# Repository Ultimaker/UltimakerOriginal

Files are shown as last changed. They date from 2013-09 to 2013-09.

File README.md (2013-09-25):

UltimakerOriginal
=================

In this repository you will find the documentation and source files for all parts in the Ultimaker-Original 3D printer. All parts are numbered. The BOM (bill of materials) directory should be your start point to find the files you need, as the BOM contains part numbers with amounts and names.
If you are missing a part or information feel free to file an issue on github.

Harma Woldhuis
Ultimaker Research and Development

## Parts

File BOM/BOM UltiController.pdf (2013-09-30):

Total quantity parts | 34
Partnummer | Naam | Quantity
1089 A2P | A | Right Side Controller | 1
1092 A2P | A | Left Side Controller | 1
1093 A2P | A | Bottom Cover Controller | 1
1095 A2P | A | Top Cover Controller | 1
1099 A1P | A | Flatcable 10 wire | 2
1129 A1P | A | Knob | 1
1135 Z1P | A | Spacer, white, 3.2x6x15 | 4
1146 Z1P | A | Ultipanel Rev 1.1 | 1
1202 Z1P | A | ISO 7380 M3x10 | 6
1207 Z1P | A | ISO 7380 M3x25 | 4
1209 Z1P | A | Nut M3 | 10
1248 Z1P | A | SD card | 1

## Ulticontroller

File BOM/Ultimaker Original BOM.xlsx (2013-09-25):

BOM | Ultimaker Original
Total quantity parts | 578
Partnummer |  |  | Naam | Quantity
1002 | A2P | A | Front Panel | 1
1003 | A2P | A | Back Panel | 1
1004 | A2P | A | Left Panel | 1
1005 | A2P | A | Right Panel | 1
1006 | A2P | A | Top Panel | 1
1007 | A2P | A | Bottom Panel | 1
1008 | A2P | A | Reel Holder Part A | 1
1009 | A2P | A | Reel Holder Mounting Plate | 1
1011 | A2P | A | Y-linear shaft | 2
1012 | A2P | A | X-linear shaft | 2
1013 | A2P | A | Feeder Base Plate Non Motor Side | 1
1014 | A1P | A | Trapezoidal Lead Nut | 1
1015 | Z1P | A | Linear Bearing LM12LUU | 2
1016 | Z1P | A | Feeder Quick Fit Coupling | 1
1017 | Z1P | A | Feeder Motor | 1
1018 | A2P | A | Feeder Base Plate Motor Side | 1
1021 | Z1P | A | Ball Bearing 688-2RS | 10
1023 | Z1P | A | Limit Switch, Black Long Wire | 1
1024 | Z1P | A | Limit Switch, Black Short Wire | 1
1025 | Z1P | A | Limit Switch, Blue Wire | 2
1026 | Z1P | A | Limit Switch, Red Wire | 2
1027 | A1P | A | Rigid Shaft Coupling | 1
1028 | A2P | A | Z-linear Shaft | 2
1029 | A2P | A | Bearing Cap Outside | 8
1031 | A2P | A | Feeder Bolt Clip | 1
1032 | A2P | A | Feeder Clamp A | 1
1033 | A2P | A | Feeder Clamp C | 1
1034 | A2P | A | Feeder Clamp B
1035 | A2P | A | Feeder Lever | 1
1036 | A2P | A | Feeder Wheel | 1
1037 | A2P | A | Print Head Coupling Plate | 1
1038 | A2P | A | Print Table Lock Nut | 4
1039 | A2P | A | Feeder U bar | 1
1041 | A2P | A | Feeder Small Gear | 1
1042 | A2P | A | Cable Strain Relief | 1
1043 | A2P | A | Trapezoidal Lead Screw | 1
1044 | A2P | A | Z-shaft Cap Top | 2
1045 | A2P | A | Bearing Cap Inside | 2
1046 | A2P | A | Print Head Shaft X,Y | 2
1047 | A2P | A | Electronics Base Plate | 1
1048 | A2P | A | Print Head Hot End Holder | 1
1049 | A2P | A | Aluminum Heater Block | 1
1052 | Z1P | A | Heater Cartridge 18V 40W | 1
1053 | A2P | A | Hot End Isolator Tube | 1
1054 | A2P | A | Nozzle 0.4mm | 1
1055 | A2P | B | Hot End Isolator Coupler | 1
1056 | A2P | B | Sintered Bushing | 4
1057 | A2P | B | Z-shaft Cap Bottom | 2
1058 | A2P | B | Print Head Back | 1
1059 | A2P | B | Print Head Top Cap | 1
1061 | A2P | B | Print Head Bottom Cap | 1
1062 | A2P | B | Print Head Left | 1
1063 | A2P | B | Print Head Front | 1
1064 | A2P | B | Print Head Right | 1
1065 | Z1P | A | Linear Bearing LM6LUU | 2
1066 | Z1P | A | Hexagon Spacer, White, M3x5.5x12 | 4
1067 | Z1P | A | PEEK Isolator | 1
1068 | Z1P | A | Thermocouple Board Spacer | 1
1069 | Z1P | A | Tube Coupling Collet | 1
1071 | Z1P | A | Clamp Clip | 1
1072 | Z1P | A | Thermocouple Transmitter | 1
1073 | Z1P | A | Thermocouple Sensor | 1
1074 | Z1P | A | Print Head Thumb Screw | 1
1075 | Z1P | A | Print Head Fan 12VDC 1,2W | 1
1076 | Z1P | A | Electronics Cooling Fan 24VDC | 1
1078 | A2P | A | Fan Duct Electronics | 1
1079 | A2P | B | Fan Duct Print Head | 1
1081 | Z1P | A | Z-Motor | 1
1082 | Z1P | A | X,Y-Motor | 2
1083 | Z1P | A | X,Y Motor Spacer Black 3.2x6x11 | 8
1084 | Z2P | A | Timing Pulley 5mm Shaft | 2
1085 | Z1P | A | Timing Belt B100 MXL | 2
1086 | Z1P | A | Timing Belt B300 MXL | 4
1087 | Z2P | A | Bowden Tube | 1
1088 | Z2P | A | Timing Pulley 8mm Shaft | 10
1090 | A1P | A | Arduino Mega Ultimaker Shield 1.5.7 | 1
1094 | A1P | A | Arduino Mega 2560 | 1
1096 | A1P | A | Power Adapter 19v-120W | 1
1097 | A1P | A | Spiral Sleeve | 1
1098 | A1P | A | Stepper Driver | 4
1101 | A2P | A | Print Table Front Plate | 1
1102 | A2P | A | Print Table Back Plate | 1
1103 | A2P | A | Trapezoidal Lead Nut Holder | 2
1104 | A2P | A | Print Table Bottom Plate | 1
1105 | A2P | A | Print Table Arm Part A | 1
1106 | A2P | A | Print Table Arm Part B | 1
1107 | A2P | A | Print Table Arm Part C1 | 4
1108 | A2P | A | Print Table Arm Part D1 | 2
1109 | A2P | A | Print Table Arm Part C2 | 4
1111 | A2P | A | Print Table Arm Part D2 | 2
1112 | A2P | A | Print Table Arm Part E | 1
1113 | A2P | A | Print Table Arm Part F | 1
1114 | A2P | A | Build Platform Acryllic | 1
1116 | A2P | A | Reel Holder Part B | 4
1117 | A2P | A | Sliding Block Part A | 8
1118 | A2P | A | Sliding Block Part B | 1
1119 | A2P | A | Sliding Block Part C | 2
1121 | A2P | A | Sliding Block Part D | 4
1122 | A2P | A | Sliding Block Part E | 1
1123 | A2P | A | Electronics Cover Plate | 1
1126 | A2P | A | Feeder Middle Plate | 1
1127 | Z1P | A | Table Spring D1450 | 1
1128 | A2P | A | Feeder Big Gear | 1
1131 | A2P | A | Cable Duct Front | 2
1132 | A2P | A | Cable Duct Back | 2
1133 | Z2P | A | Feeder Knurled Bolt | 1
1134 | Z1P | A | Capnut M8 | 1
1136 | Z1P | A | Washer M8 | 3
1137 | Z1P | A | Nut M8 | 1
1139 | Z1P | A | Spacer, White, 3.2x5x16 | 4
1141 | Z1P | A | Lock Nut M3 | 11
1142 | Z1P | A | Ball Bearing 693ZZ | 1
1143 | Z1P | A | Feeder Spring D2110 | 1
1144 | Z1P | A | USB Cable | 1
1145 | A2A | A | Main Cable | 1
1147 | Z1P | A | Power Cable EU Type C6
1148 | Z1P | A | Power Cable UK Type C6
1149 | Z1P | A | Power Cable AU Type C6
1150 | Z1P | A | Power Cable US Type C6
1201 | Z1P | B | Washer Large M3 | 7
1202 | Z1P | B | ISO 7380 M3x10 | 45
1203 | Z1P | B | ISO 7380 M3x12 | 5
1204 | Z1P | B | ISO 7380 M3x16 | 67
1206 | Z1P | B | ISO 7380 M3x20 | 12
1207 | Z1P | B | ISO 7380 M3x25 | 1
1208 | Z1P | B | ISO 7380 M3x30 | 53
1209 | Z1P | B | Nut M3 | 151
1211 | Z1P | A | Set Screw M4x4 | 12
1212 | Z1P | A | Set Screw M3x5 | 5
1225 | Z1P | A | tape | 1
1226 | Z1P | A | grease | 1
1227 | Z1P | A | Hex Key Srewdriver 2 | 1
1400 | Z1P | A | Hex Key Wrench 1.5 | 1

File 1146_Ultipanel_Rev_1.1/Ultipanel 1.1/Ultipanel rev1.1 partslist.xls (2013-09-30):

Part | RS partno | Manufacturer partno | Value | Device | Package | Remarks
724-3175 | 724-3175 | RS 724-3175 |  |  |  | buzzer
DS1 | 532-6818 | Displaytech 204A-CC-BC-3LP |  |  |  | lcd screen Blue/White, soldered with header 2.54 mm
EC11E15244B2 | 729-5609 | ALPS EC11E15244B2 |  |  |  | 20mm Vertical encoder 15 Pulses 30 DET
EXP1 | 473-8349 | TE connectivity 1-1634689-0 |  |  |  | right angle!
EXP2 | 473-8349 | TE connectivity 1-1634689-0 |  |  |  | right angle!
HRS163_REVERSE | 685-0788 | Hirose DM1B-DSF-PEJ(82)
R3 | 731-2883 | Panasonic EVM3YSX50B14 | 10K
RBEEP | 708-6014 |  | 440R |  | 0805
RLED | 721-9725 |  | 68R |  | 1206
SHIFT | 483-6544P | NXP 74HC4050D | 4050D |  |  | levelshifter
T4 | 294-312 | Magnatec 2N3904 | 2N3904
JP1 | not used

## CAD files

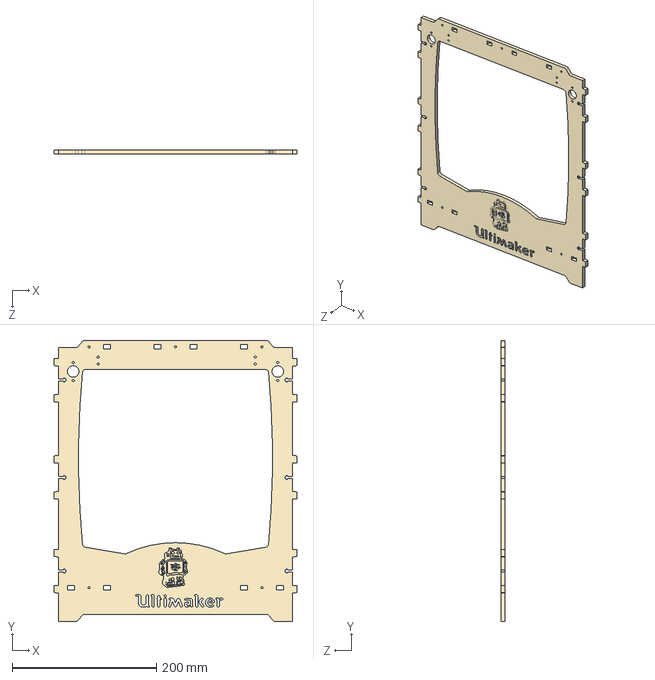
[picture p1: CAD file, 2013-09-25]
1002_Front_Panel/1002-A2P-A.STEP
337.2 x 390.0 x 6.00 mm

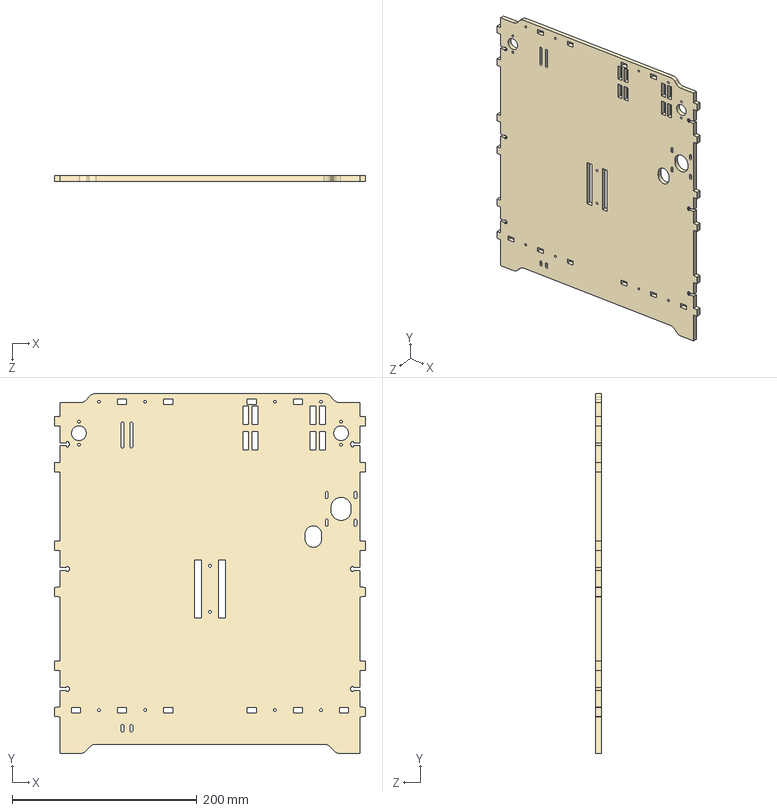
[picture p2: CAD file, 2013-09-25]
1003_Back_Panel/1003-A2P-A.STEP
337.2 x 390.0 x 6.00 mm

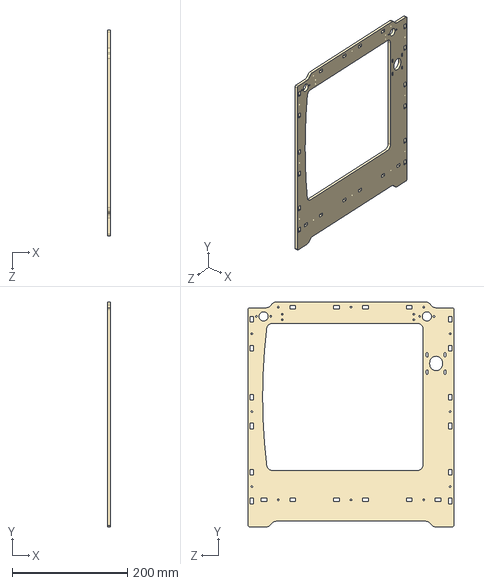
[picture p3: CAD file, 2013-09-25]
1004_Left_Panel/1004-A2P-A.STEP
6.00 x 390.0 x 357.0 mm

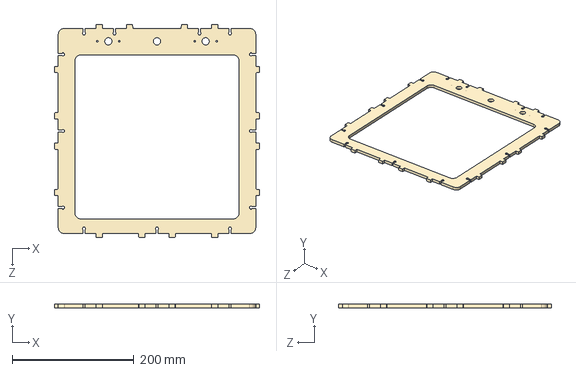
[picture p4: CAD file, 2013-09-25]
1006_Top_Panel/1006-A2P-A.STEP
337.2 x 6.00 x 349.7 mm

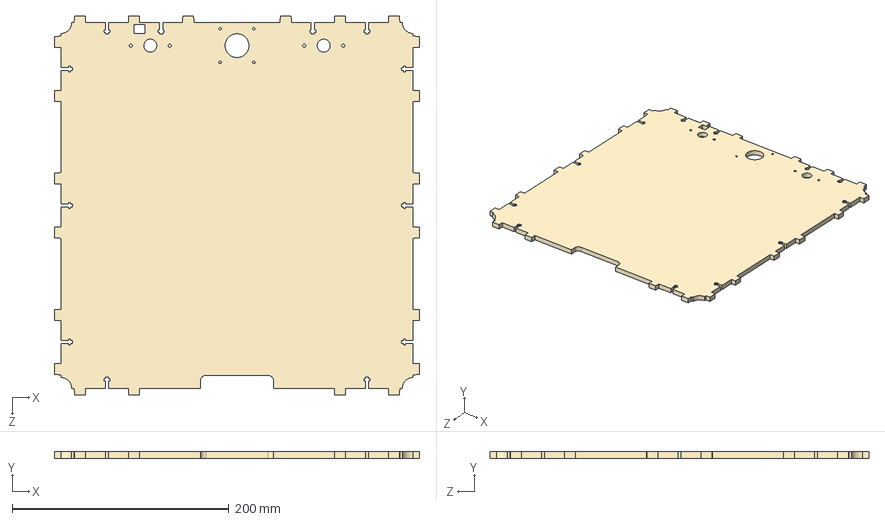
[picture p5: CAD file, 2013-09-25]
1007_Bottom_Panel/1007-A2P-A.STEP
337.2 x 6.00 x 349.7 mm

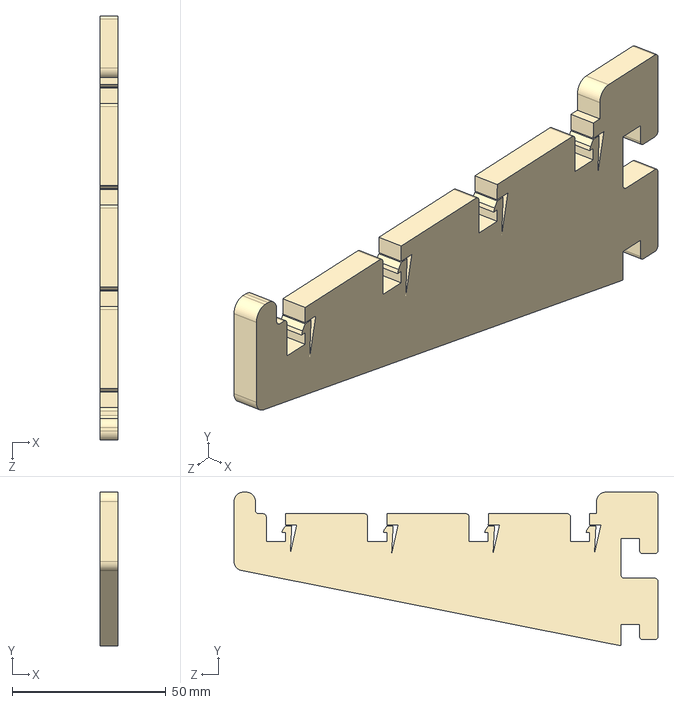
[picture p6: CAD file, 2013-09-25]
1008_Reel_Holder_Part_A/1008-A2P-A.STEP
6.00 x 50.0 x 138.0 mm

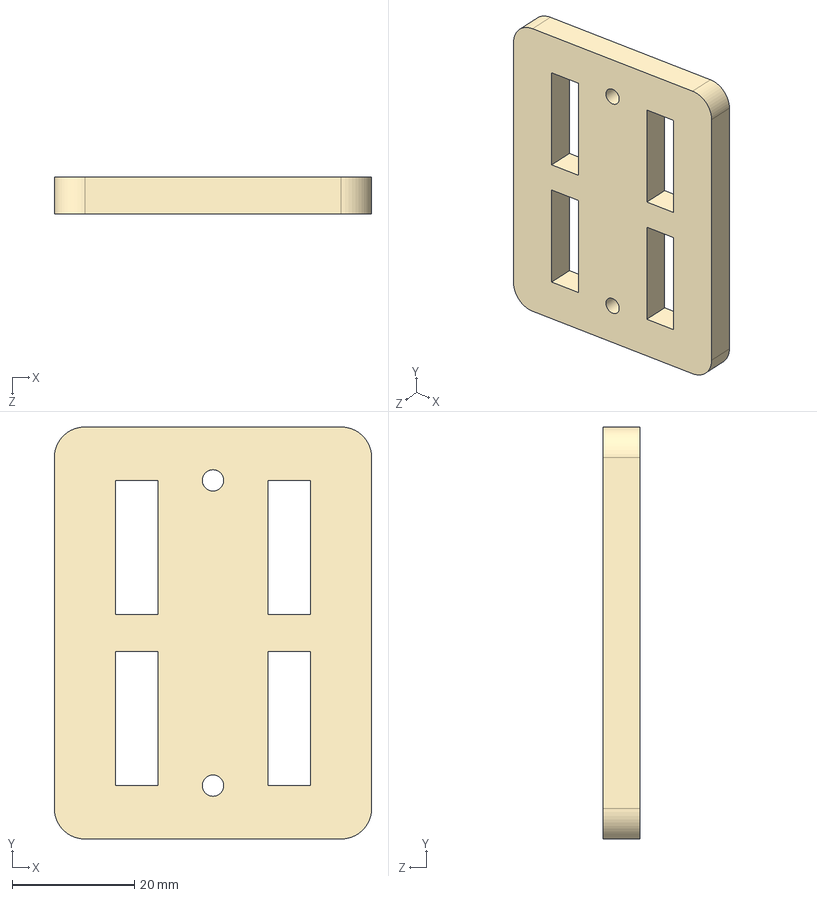
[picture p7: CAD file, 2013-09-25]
1009_Reel_Holder_Mounting_Plate/1009-A2P-A.STEP
52.0 x 67.5 x 6.00 mm

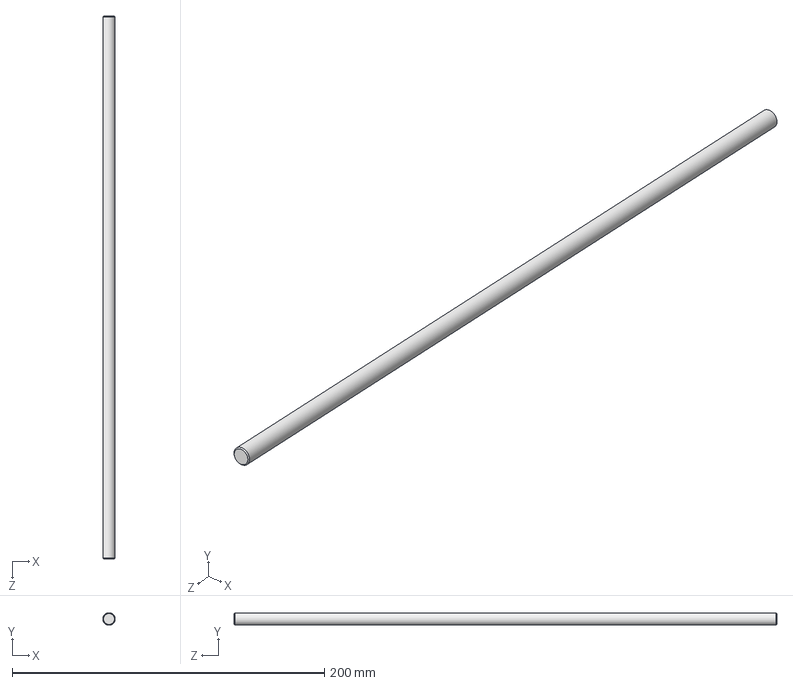
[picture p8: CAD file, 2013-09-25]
1011_Y-linear_shaft/1011-A2P-A.STEP
7.99 x 8.00 x 348.0 mm

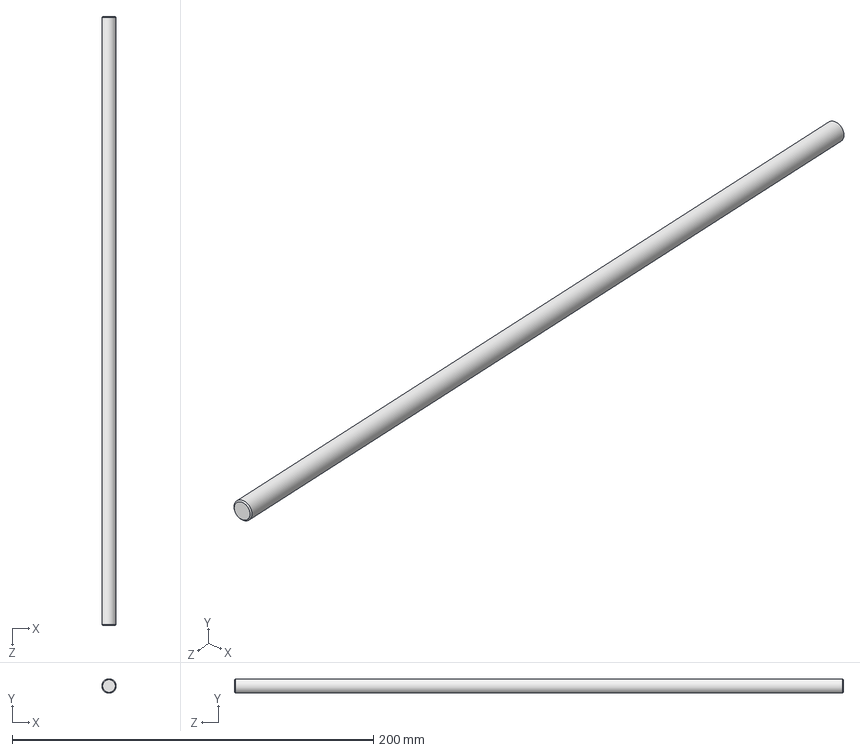
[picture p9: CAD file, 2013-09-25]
1012_X-linear_shaft/1012-A2P-A.STEP
7.99 x 8.00 x 337.0 mm

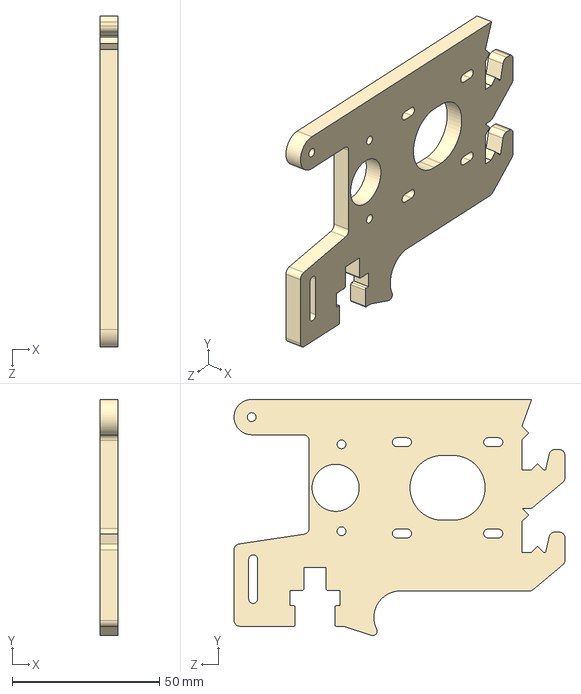
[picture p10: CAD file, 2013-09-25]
1013_Feeder_Base_Plate_Non_Motor_Side/1013-A2P-A.STEP
6.00 x 80.1 x 112.4 mm

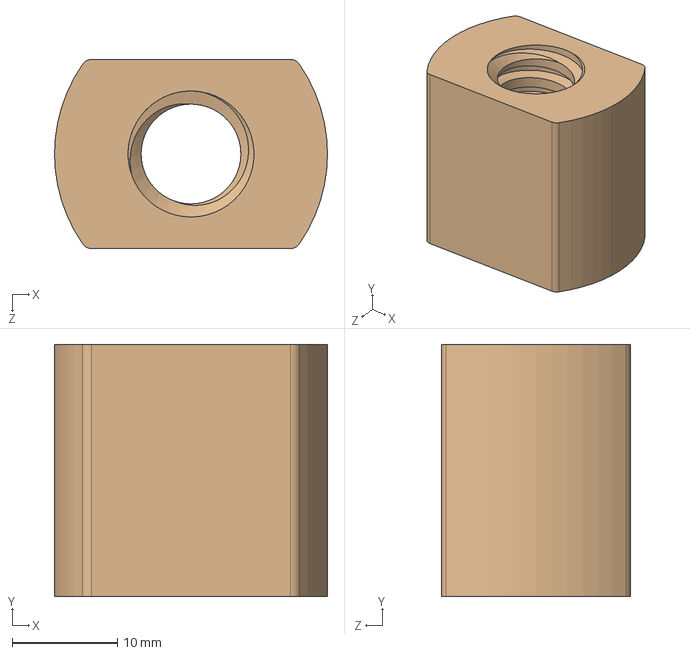
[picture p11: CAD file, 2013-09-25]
1014_Trapezoidal_Lead_Nut/1014-A1P-A.STEP
26.0 x 24.0 x 18.0 mm

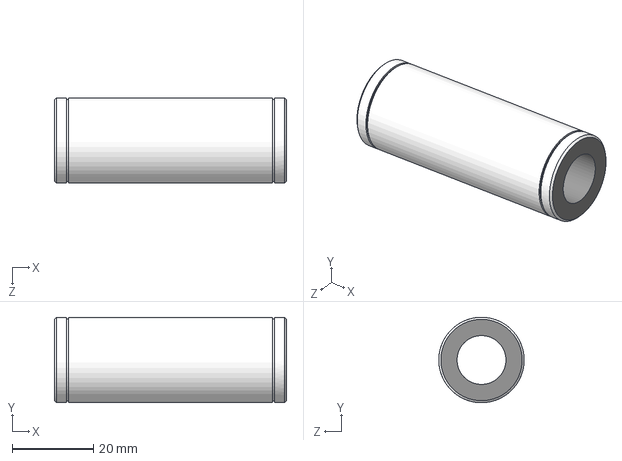
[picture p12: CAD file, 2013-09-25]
1015_Linear_Bearing_LM12LUU/1015-Z1P-A.STEP
57.0 x 21.0 x 21.0 mm

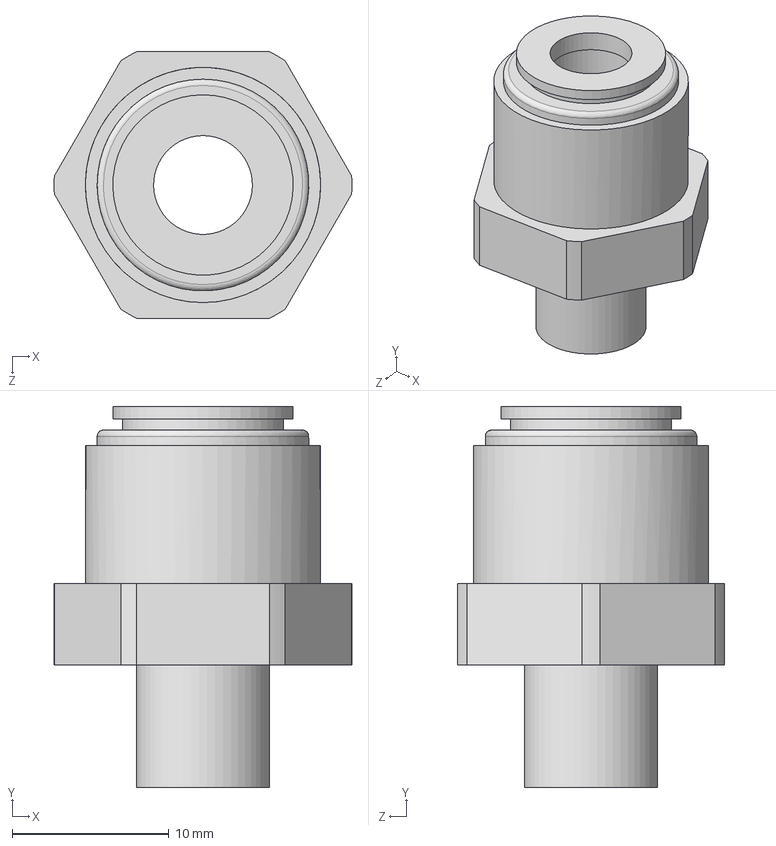
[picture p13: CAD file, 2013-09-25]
1016_Feeder_Quick_Fit_Coupling/1016-Z1P-A.STEP
19.0 x 24.3 x 17.0 mm

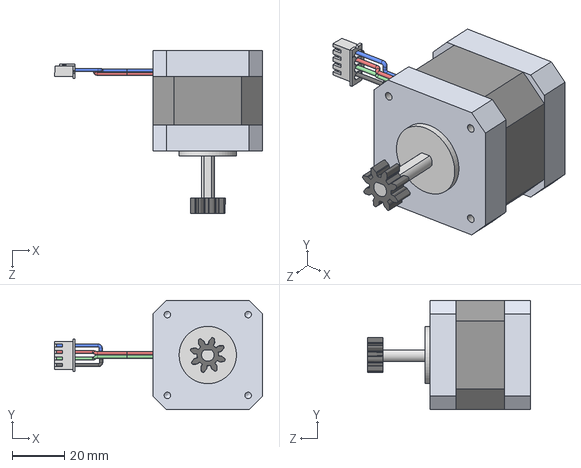
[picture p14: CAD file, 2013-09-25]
1017_Feeder_Motor/1017-Z1P-A.STEP
79.8 x 42.0 x 62.5 mm

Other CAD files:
1005_Right_Panel/1005-A2P-A.STEP
1018_Feeder_Base_Plate_Motor_Side/1018-A2P-A.STEP
1021_Ball_Bearing_688-2RS/1021-Z1P-A.STEP
1023_Limit_Switch,_Black_Long_Wire/1023-Z1P-A.STEP
1024_Limit_Switch,_Black_Short_Wire/1024-Z1P-A.STEP
1025_Limit_Switch,_Blue_Wire/1025-Z1P-A.STEP
1026_Limit_Switch,_Red_Wire/1026-Z1P-A.STEP
1027_Rigid_Shaft_Coupling/1027-A1P-A.STEP
1028_Z-linear_Shaft/1028-A2P-A.STEP
1029_Bearing_Cap_Outside/1029-A2P-A.STEP
1031_Feeder_Bolt_Clip/1031-A2P-A.STEP
1032_Feeder_Clamp_A/1032-A2P-A.STEP
1033_Feeder_Clamp_C/1033-A2P-A.STEP
1034_Feeder_Clamp_B/1034-A2P-A.STEP
1035_Feeder_Lever/1035-A2P-A.STEP
1036_Feeder_Wheel/1036-A2P-A.STEP
1037_Print_Head_Coupling_Plate/1037-A2P-A.STEP
1038_Print_Table_Lock_Nut/1038-A2P-A.STEP
1039_Feeder_U_bar/1039-A2P-A.STEP
1041_Feeder_Small_Gear/1041-A2P-A.STEP
1042_Cable_Strain_Relief/1042-A2P-A.STEP
1043_Trapezoidal_Lead_Screw/1043-A2P-A.STEP
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

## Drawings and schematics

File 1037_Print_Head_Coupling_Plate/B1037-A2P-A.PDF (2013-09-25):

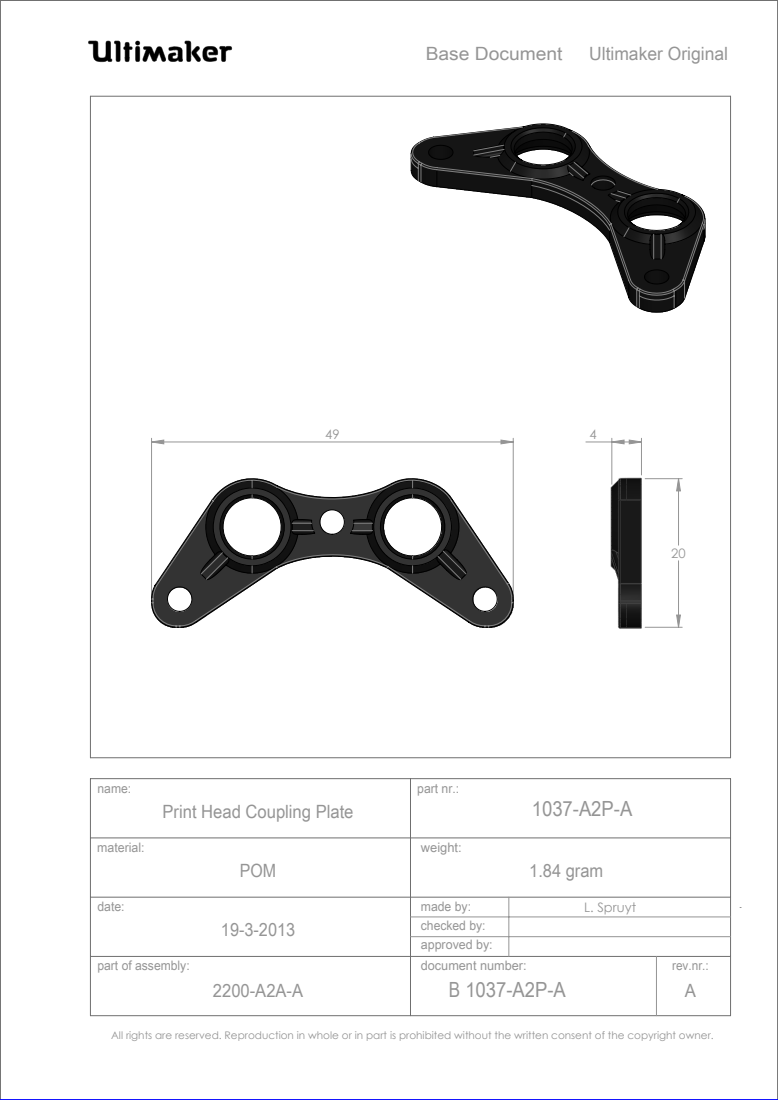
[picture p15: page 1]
POM; 1.84 gram; Ultimaker Original; part of assembly:; rev.nr.:; part nr.:; made by:; Base Document; approved by:; checked by:; L. Spruyt; document number: B 1037-A2P-A

name:
Print Head Coupling Plate

All rights are reserved. Reproduction in whole or in part is prohibited without the written consent of the copyright owner.

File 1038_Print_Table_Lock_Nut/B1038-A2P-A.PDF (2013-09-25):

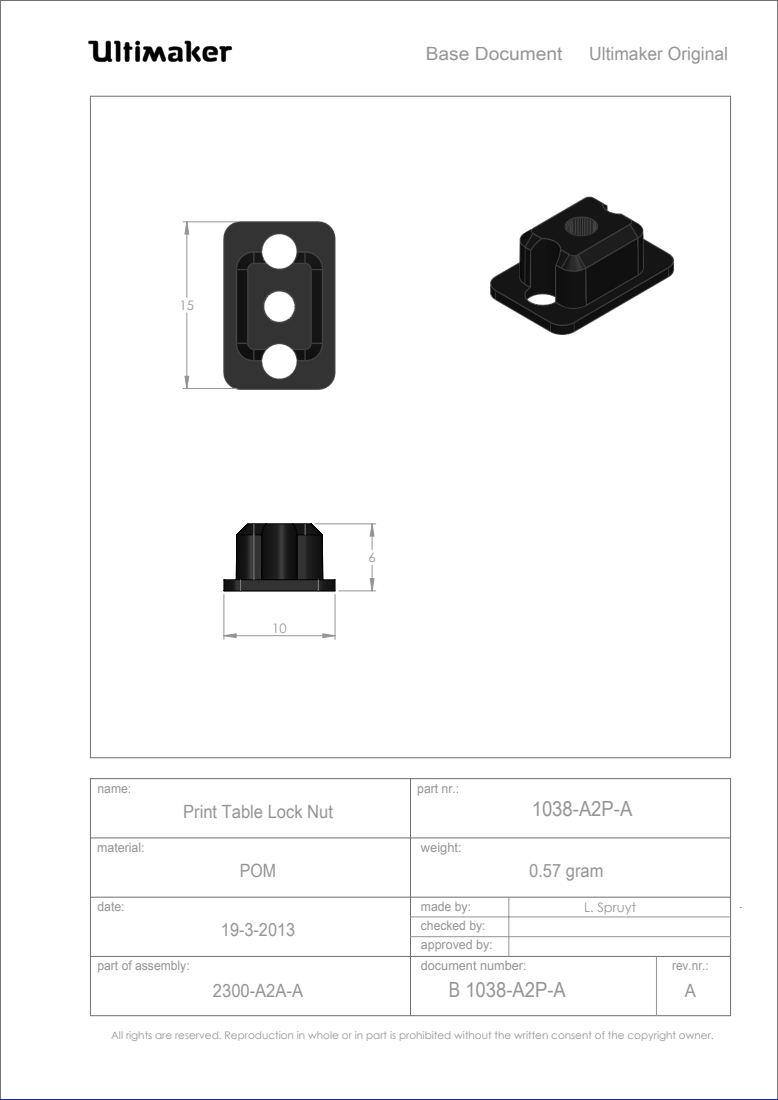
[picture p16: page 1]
POM; 0.57 gram; Ultimaker Original; part of assembly:; rev.nr.:; part nr.:; made by:; Base Document; approved by:; checked by:; L. Spruyt; document number: B 1038-A2P-A

Print Table Lock Nut

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

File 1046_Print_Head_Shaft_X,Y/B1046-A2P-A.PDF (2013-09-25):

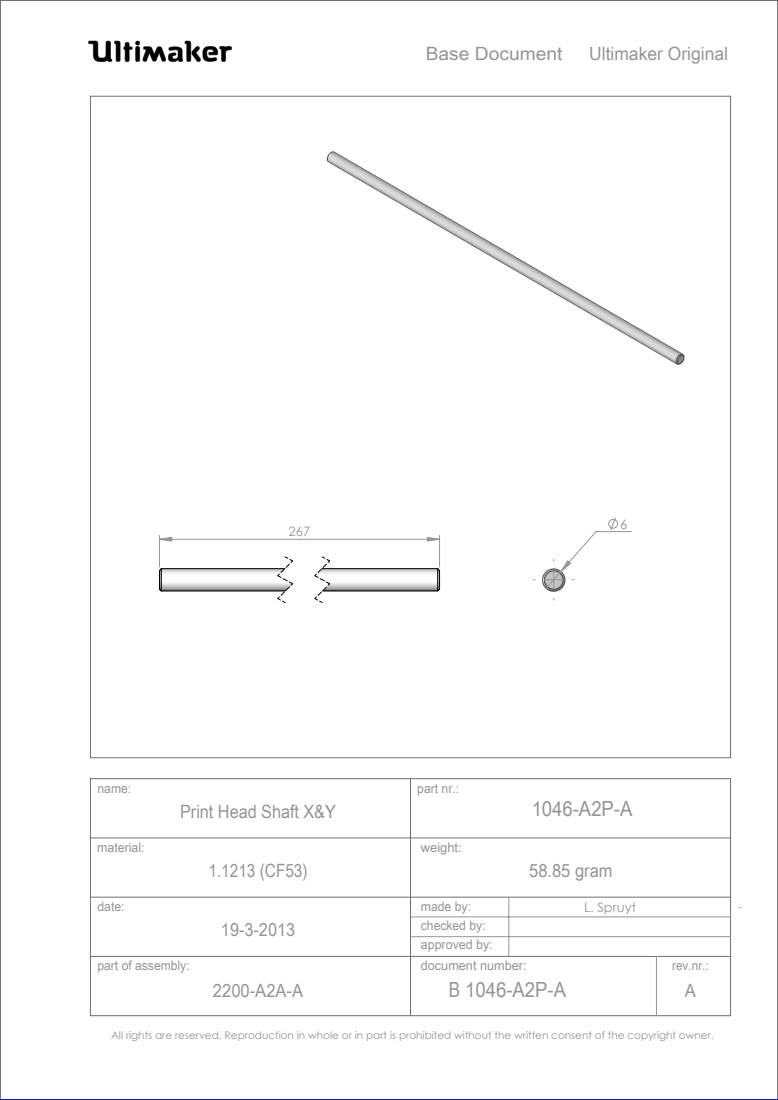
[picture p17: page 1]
58.85 gram; Ultimaker Original; part of assembly:; rev.nr.:; part nr.:; made by:; Base Document; approved by:; checked by:; L. Spruyt; document number: B 1046-A2P-A

Print Head Shaft X&Y

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

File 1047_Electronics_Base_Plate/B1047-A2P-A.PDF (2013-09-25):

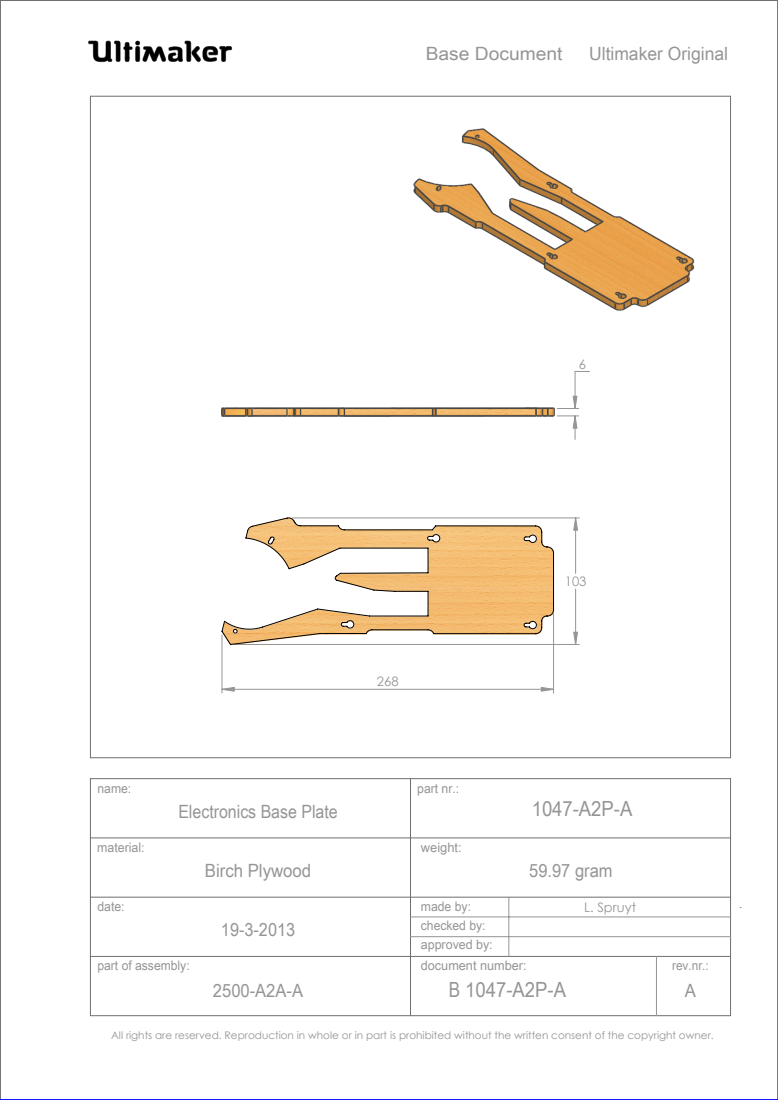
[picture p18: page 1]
Birch Plywood; 59.97 gram; Ultimaker Original; part of assembly:; rev.nr.:; part nr.:; made by:; Base Document; approved by:; checked by:; L. Spruyt; document number: B 1047-A2P-A

Electronics Base Plate

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

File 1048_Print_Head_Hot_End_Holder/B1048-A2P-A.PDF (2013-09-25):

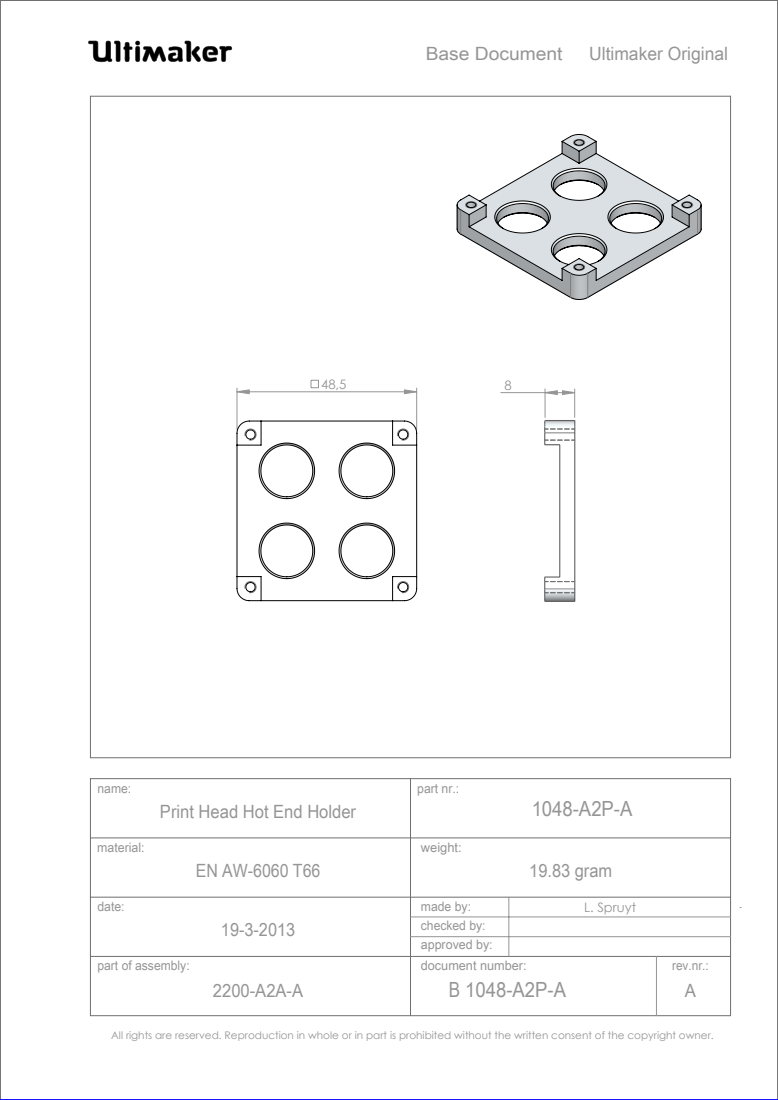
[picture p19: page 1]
19.83 gram; Ultimaker Original; part of assembly:; rev.nr.:; part nr.:; made by:; Base Document; approved by:; checked by:; L. Spruyt; document number: B 1048-A2P-A

name:
Print Head Hot End Holder

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

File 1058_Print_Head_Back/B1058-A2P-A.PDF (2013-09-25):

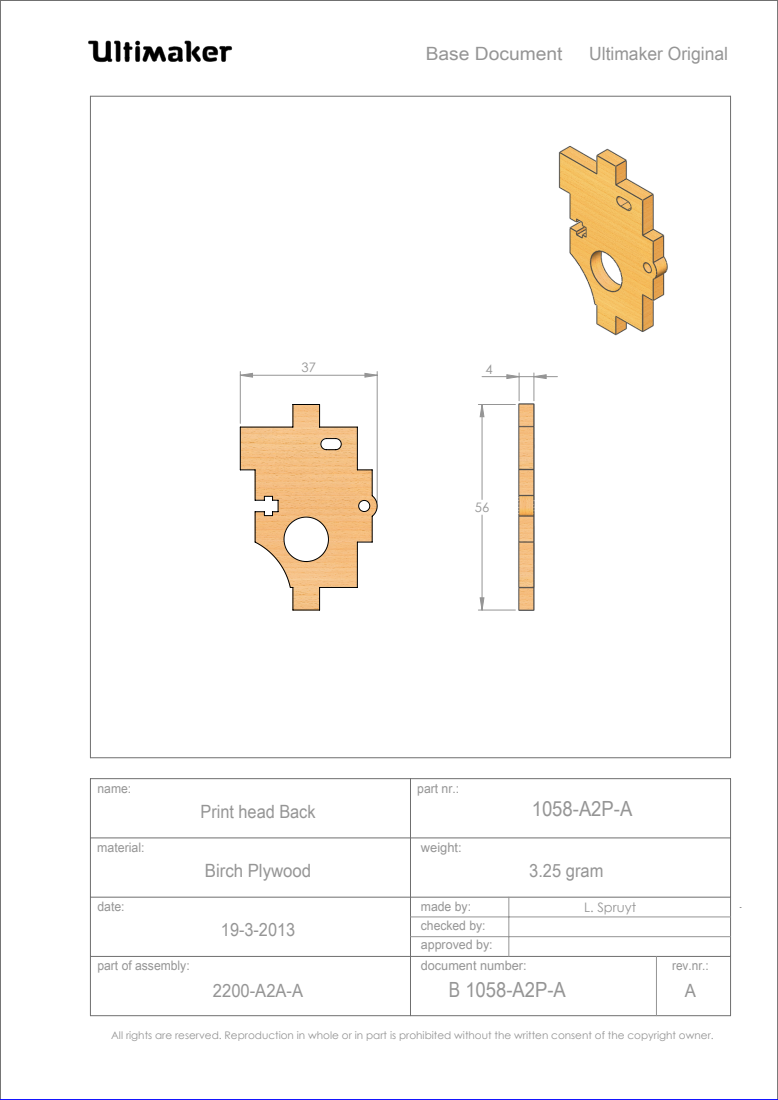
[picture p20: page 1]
Birch Plywood; 3.25 gram; Ultimaker Original; part of assembly:; rev.nr.:; part nr.:; made by:; Base Document; approved by:; checked by:; L. Spruyt; document number: B 1058-A2P-A

Print head Back

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

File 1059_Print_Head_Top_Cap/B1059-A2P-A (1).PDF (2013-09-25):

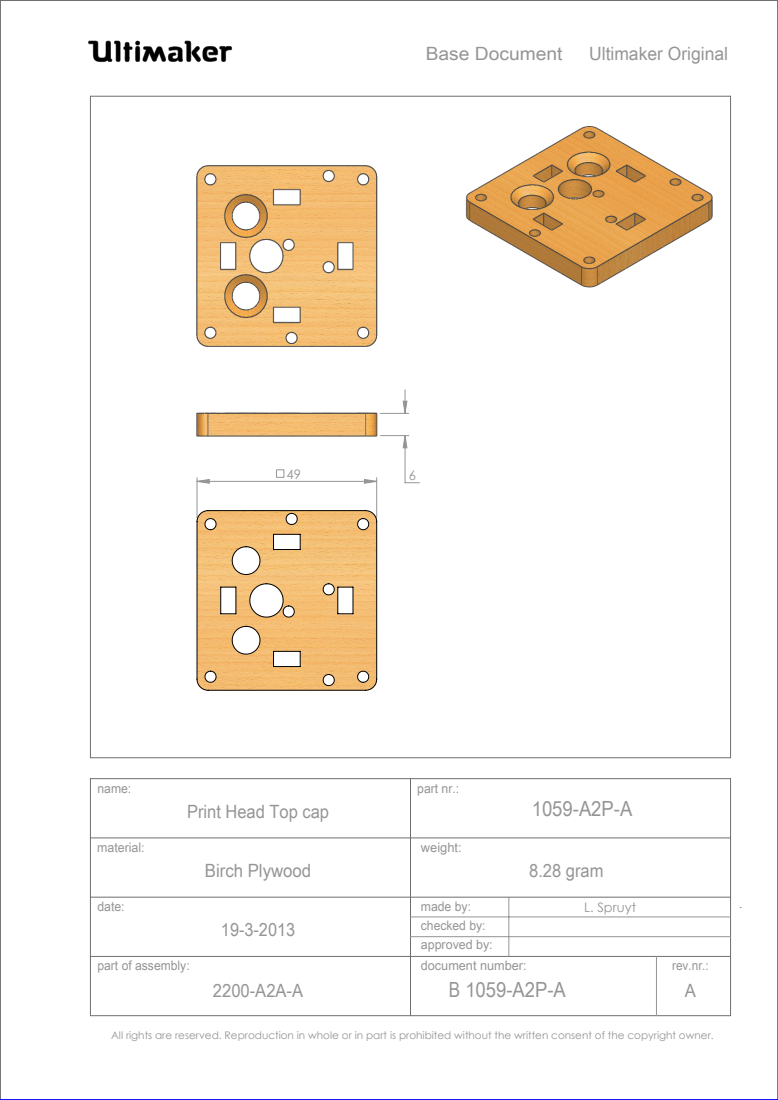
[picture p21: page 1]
Birch Plywood; 8.28 gram; Ultimaker Original; part of assembly:; rev.nr.:; part nr.:; made by:; Base Document; approved by:; checked by:; L. Spruyt; document number: B 1059-A2P-A

Print Head Top cap

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

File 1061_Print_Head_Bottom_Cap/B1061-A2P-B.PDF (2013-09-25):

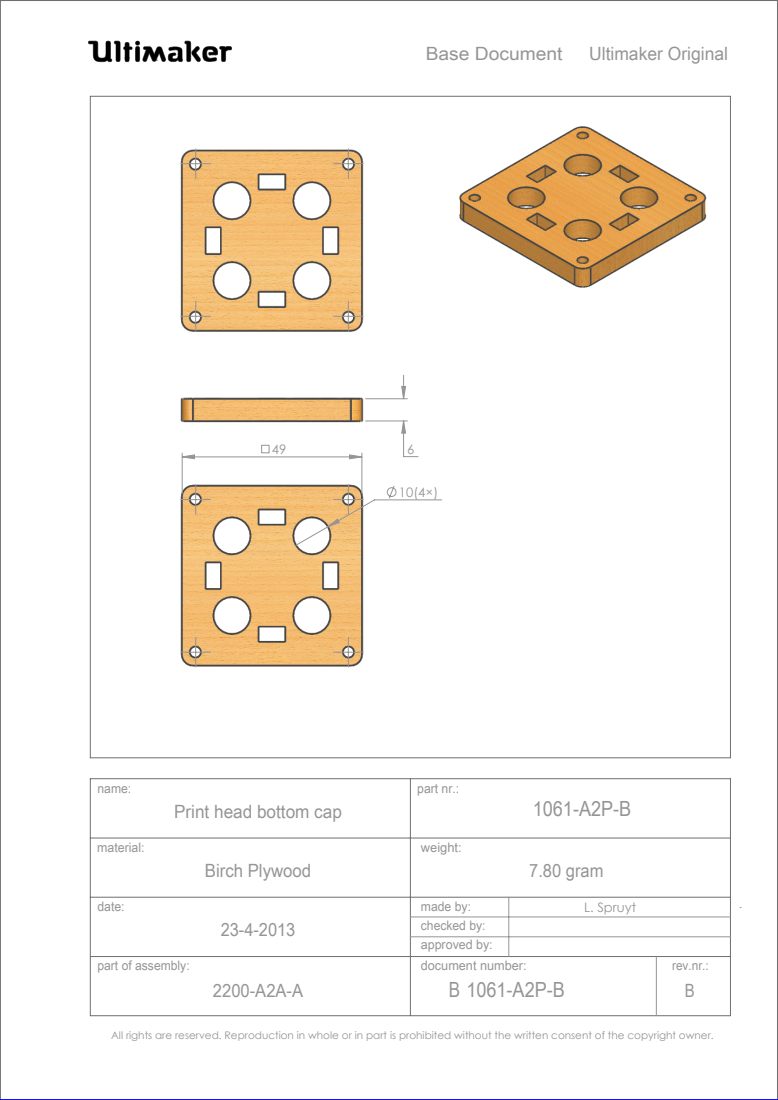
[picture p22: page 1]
Birch Plywood; 7.80 gram; Ultimaker Original; part of assembly:; rev.nr.:; part nr.:; made by:; Base Document; approved by:; checked by:; L. Spruyt; document number: B 1061-A2P-B

Print head bottom cap

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

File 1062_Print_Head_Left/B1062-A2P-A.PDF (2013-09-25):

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

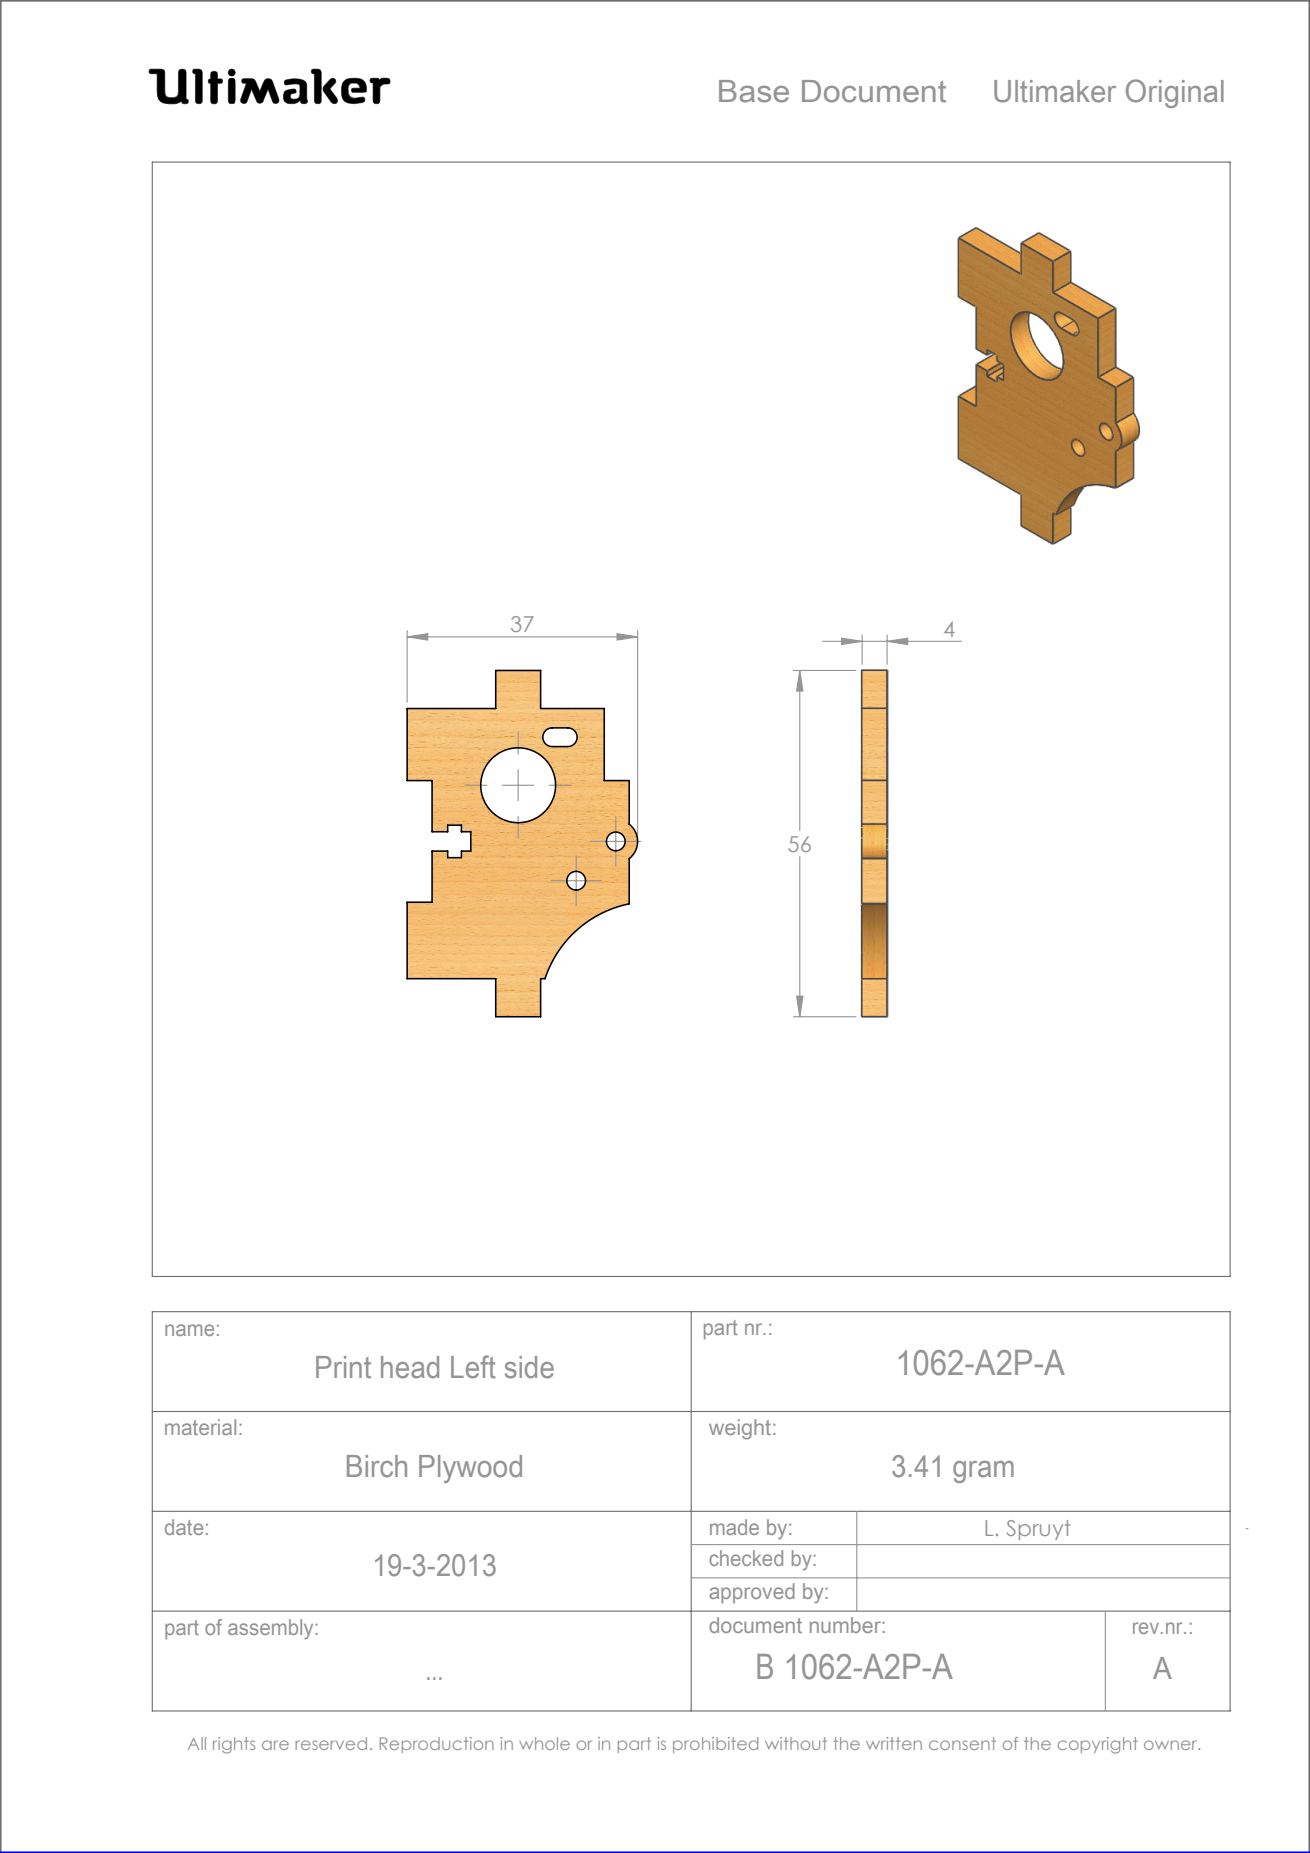
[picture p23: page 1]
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

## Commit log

2013-09-25 initial commit
    first upload with all parts
    [1002-A2P-A.STEP, 1003-A2P-A.STEP, 1004-A2P-A.STEP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]
2013-09-25 Updated readme to notify people of the BOM.
2013-09-26 laserfiles
    laserfiles for the Ultimaker original and the dual extrusion upgrade
2013-09-30 thermocouple board and UM shield electronic files
    [Arduino MEGA Ultimaker Shield v1.5.4.brd, Arduino MEGA Ultimaker Shield v1.5.4.sch, Arduino MEGA Ultimaker Shield v1.5.5.brd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]
2013-09-30 Parts and BOM of UltiController
    [1089-A2P-A.STEP, 1092-A2P-A.STEP, 1093-A2P-A.STEP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]
2013-09-30 Updated directory names to contain part names from BOM.
    [1002-A2P-A.STEP, 1003-A2P-A.STEP, 1004-A2P-A.STEP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]
2013-09-30 Updated directory names.
    [1002-A2P-A.STEP, 1003-A2P-A.STEP, 1004-A2P-A.STEP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]
2013-10-28 stepper driver files
    the stepper driver files can be found in the folder 1098 stepper driver
    [A4988.PrjPCB]
2013-10-28 stepper driver file
    the pdf overview file
2013-10-30 ulticontroller lasercutdrawings
    the lasercutdrawings for the ulticontroller
2013-10-30 lasercutdrawings ulticontroller
    this time with extension...
2013-11-11 old lasercutdrawings
    1158 ultimaker drawings (old)
2014-09-12 Added step files for dual extrusion lasercut parts, see http://umforum.ultimaker.com/index.php?/topic/7215-where-i-find-the-drawings-for-the-2-extruder-kit/
    [1190-A2P-A.STEP, 1191-A2P-A.STEP, 1192-A2P-A.STEP]
